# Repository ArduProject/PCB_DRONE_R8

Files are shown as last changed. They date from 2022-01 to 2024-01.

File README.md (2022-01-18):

# Archivos de fabricación de la versión del PCB con STM32F103R8

CURSO_PCB_DRONE

En este repositorio encontrareis los archivos de fabricación y las listas de montaje del PCB con STM32F103**R8** que hemos visto en el curso. Enlace al curso: https://www.udemy.com/course/controlador-de-vuelo-drones-arduino-pcb/?referralCode=FD3F1CBF871EDFD84B6F

La estructura de las carpetas de este repositorio es la misma que hemos visto en el curso: una carpeta GERBER con los archivos de fabricación del PCB, y una carpeta MONTAJE con las listas de componentes y el archivo de colocación de huellas (CURSO_PCB_DRONE-all-pos.xlsx). Tambien se incluye un manual de montaje del PCB y del drone. La única diferencia con el curso es que al descargar el repositorio, dentro de la carpeta MONTAJE encontrareis dos listas en vez de una:

- Lista de componentes (BOM) para cargar en la web de JLCPCB, la lista que hemos generado en el vídeo anterior: CURSO_PCB_DRONE_BOM_JLCPCB.xlsx
- Lista con los componentes que tendremos que comprar y montar en el PCB y el drone (antena SMA, conector de batería XT60, motores, batería...): CURSO_PCB_DRONE_BOM_extra.xlsx

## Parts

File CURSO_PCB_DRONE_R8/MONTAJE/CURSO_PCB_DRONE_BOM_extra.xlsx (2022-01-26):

Id | Referencia esquema | Descripción | Enlace Amazon | Enlace Aliexpress | Necesario para montaje de:
 |  |  |  |  | PCB | DRONE
A1 | J16 | Antena SMA | https://amzn.to/3mPTdu5 | https://s.click.aliexpress.com/e/_9z2YgC | X
A2 | J17 | Conector de batería XT60 | https://amzn.to/3zj09VF | https://s.click.aliexpress.com/e/_Al7UrO | X | X
A3 | U11 | Regulador LM7805 TO-220 | https://amzn.to/3HzEs6F | https://s.click.aliexpress.com/e/_ATJGEc | X
A4 | J2, J4, J6, J7, J8, J9, J10, J11, J12, J13, J14, J15 | Kit conectores 'pin header' macho de 2.54mm | https://amzn.to/3ES77Su | https://s.click.aliexpress.com/e/_9vqOJA | X
A5 | - | Kit conectores 'pin socket' hembra de 2.54mm | https://amzn.to/3qSfYP1 | https://s.click.aliexpress.com/e/_AmZCtw | X | X
A6 | SW4 | Interruptor manual ref. SS-12D00G4 | https://amzn.to/3pXzwlO | https://s.click.aliexpress.com/e/_9zbXPK | X
A7 | J5 | Monitor OLED 0.96' | - | https://s.click.aliexpress.com/e/_AbfWzS | X
A8 | - | Separadores de plástico 6mm M3 | https://amzn.to/3FL1Zkq | https://s.click.aliexpress.com/e/_AnLr04 | X | X
A9 | - | Tuercas de plástico M3 | https://amzn.to/3FL1Zkq | https://s.click.aliexpress.com/e/_ASSfpm | X | X
A10 | - | Tornillos de plástico 4mm M3 | https://amzn.to/3FL1Zkq | https://s.click.aliexpress.com/e/_A4Ar1A | X | X
A11 | - | Kit de 4 motores MT2204 2300KV + ESC 12A + Hélices 5030 | - | https://s.click.aliexpress.com/e/_9x4l8y |  | X
A12 | - | Mando FLYSKY-FS-i6 + receptor iA6B | https://amzn.to/34aDmQd | https://s.click.aliexpress.com/e/_Aa8E8Y |  | X
A13 | - | Frame 250mm | - | https://s.click.aliexpress.com/e/_9jW9De |  | X
A14 | - | Batería Lipo 3S 11.1V 1800mAh 50C XT60 | https://amzn.to/3f0Io4d | https://s.click.aliexpress.com/e/_9uFewy |  | X
A15 | - | LiDAR FT-LUNA | - | https://s.click.aliexpress.com/e/_ALu5SY |  | X
A16 | - | Barómetro MS5611 | https://amzn.to/34iogs3 | https://s.click.aliexpress.com/e/_9ydlqC |  | X
A17 | - | Carcasa MS5611 (modelo 3D) | https://www.thingiverse.com/thing:3460451 |  |  | X
A18 | - | Terminales bala 3.5mm | https://amzn.to/34gPRKd | https://s.click.aliexpress.com/e/_9Qs85a |  | X
A19 | - | Tuerca de acero inox. M3 | - | https://s.click.aliexpress.com/e/_A7q36C |  | X
A20 | - | Tornillo de acero inox. 8mm M3 | - | https://s.click.aliexpress.com/e/_AfkXxE |  | X
A21 | - | Conector terminal anillo RV1.25-3 | - | https://s.click.aliexpress.com/e/_AePFNA |  | X
A22 | - | Cable AWG 30 | https://amzn.to/3qNt8gp | https://s.click.aliexpress.com/e/_97MU5K |  | X

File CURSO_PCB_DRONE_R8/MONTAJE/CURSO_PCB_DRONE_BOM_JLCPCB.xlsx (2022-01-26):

Designator | Footprint | Comment | JLCPCB Part #
Y3 | Crystal_SMD_5032-2Pin_5.0x3.2mm | 8Mhz | C115962
J3,J1 | MICRO-USB-SMD_5P-P0.65-H-F_MICRO5.9MMUSB | USB_B_Micro | C393940
Y2 | Crystal_SMD_3225-4Pin_3.2x2.5mm | 12Mhz | C9002
U7 | TF-SMD_472192001 | MICROSD_C164170 | C164170
U10 | InvenSense_QFN-24_4x4mm_P0.5mm | MPU-6050 | C24112
C43,C28,C29,C30 | C_0402_1005Metric | 10nF | C15195
U4 | LQFP-64_10x10mm_P0.5mm | STM32F103R8T6 | C46034
U1 | SOIC-16_3.9x9.9mm_P1.27mm | CH340G | C14267
C1,C2,C4,C5,C6,C10,C11,C12,C14,C15,C16,C19,C22,C23,C24,C33,C39,C44,C45,C46,C8,C9 | C_0402_1005Metric | 100nF | C1525
C3,C7,C40 | C_0402_1005Metric | 4.7uF | C23733
C13,C27 | C_0402_1005Metric | 1uF | C52923
C17,C18,C35,C36 | C_0402_1005Metric | 12pF | C1547
C20,C21 | C_0402_1005Metric | 33pF | C1562
C25,C26 | C_0402_1005Metric | 20pF | C1554
C31,C32 | C_0402_1005Metric | 10pF | C32949
C34 | C_0402_1005Metric | 33nF | C1585
C37 | C_0402_1005Metric | 1.5pF | C1552
C38 | C_0402_1005Metric | 1pF | C1550
C41,C47 | C_0402_1005Metric | 2.2nF | C1531
C42 | C_0402_1005Metric | 4.7pF | C1569
C48 | C_1206_3216Metric | 0.22uF | C1857
C49 | C_1206_3216Metric | 10uF | C13585
C50,C51 | C_1206_3216Metric | 10uF (t) | C7171
D3,D4,D5,D12,D13 | LED_0603_1608Metric | ROJO | C2286
D6,D7,D15 | LED_0603_1608Metric | AZUL | C72041
D8,D10,D11,D14,D16 | LED_0603_1608Metric | VERDE | C72043
FB1,FB2 | L_0805_2012Metric | 100Ohm @ 100Mhz | C1015
L1 | L_0402_1005Metric | 27nH | C18830
L2 | L_0402_1005Metric | 3.9nH | C14033
L3 | L_0402_1005Metric | 8.2nH | C16208
L4 | L_0402_1005Metric | 2.7nH | C27123
R1,R2 | R_0402_1005Metric | 1k | C11702
R11,R12,R13,R30,R31,R33,R34,R19 | R_0402_1005Metric | 10k | C25744
R14 | R_0402_1005Metric | 1.5k | C25867
R15 | R_0402_1005Metric | 330 | C25104
R20,R21 | R_0603_1608Metric | 1.5k | C22843
R22,R23,R24,R18 | R_0603_1608Metric | 1k | C21190
R25,R26,R27,R28,R39 | R_0402_1005Metric | 4.7k | C25900
R35 | R_0402_1005Metric | 22k | C25768
R36 | R_0402_1005Metric | 1M | C26083
SW1,SW2,SW3 | KEY-TH_2P-L6.0-W3.5-P6.50 | RST | C221867
U2 | TQFP-32_7x7mm | ATMEGA328P-AU | C14877
U3 | SOIC-8_W3.9mm | LM358DR | C7950
U5 | QFN-20-1EP_4x4mm_P0.5mm_EP2.5x2.5mm | nRF24L01P | C8791
U6 | SOIC-20W_7.5x12.8mm_P1.27mm | 74HC245 | C5625
U8 | SOT-23-6 | SRV05-4 | C85364
U9 | SOT-353_SC-70-5 | 74AHC1G125 | C151890
U12 | SOT-223-3_TabPin2 | AMS1117-3.3 | C6186
Y1,Y5 | Crystal_SMD_3225-4Pin_3.2x2.5mm | 16Mhz | C13738
Y4 | Crystal_SMD_2012-2Pin_2.0x1.2mm | 32.768kHz | C97602
R9,R10,R16,R17 | R_0603_1608Metric | 22 | C23345
R37 | R_0603_1608Metric | 4.7k | C23162
R3,R4,R5 | R_0603_1608Metric | 750 | C23241
R6,R7,R8,R38 | R_0603_1608Metric | 220 | C22962
R29 | R_0603_1608Metric | 47k | C25819
R32 | R_0603_1608Metric | 15k | C22809
D1,D2,D9 | D_SOD-123 | B5819W | C8598

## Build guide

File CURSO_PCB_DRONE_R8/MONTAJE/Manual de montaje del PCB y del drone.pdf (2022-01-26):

# Manual de montaje del PCB

No todos los componentes del PCB vienen montados desde JLCPCB. Para reducir el coste del PCB, hay algunos componentes que tenemos que comprar y soldar nosotros mismo en casa. En los siguientes apartados veremos como montar estos componentes. En cada apartado se especifica que componente de la lista CURSO_PCB_DRONE_BOM_extra.xlsx hay que utilizar en cada caso.

## 1- Conectores de señal

El PCB cuenta con varios conectores que tenemos que soldar nosotros mismos. Utilizaremos el mismo tipo de conector en todos los casos (Id. A4). Lo ideal es comprar una o varias tiras de este conector e ir cortándolo y soldándolo a la medida de cada caso:

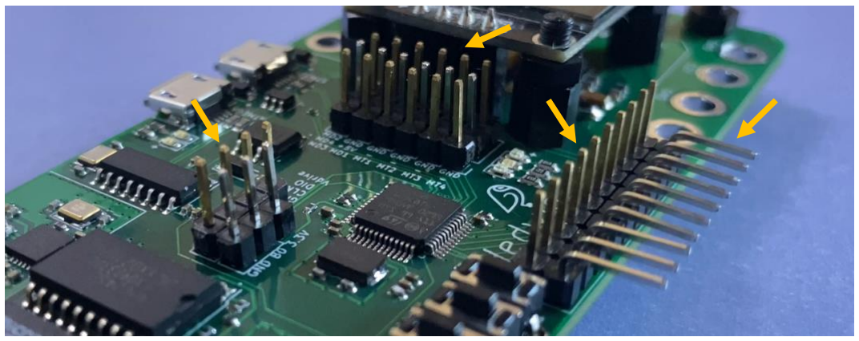
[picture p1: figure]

En lugar del conector con inclinación de 90º se puede utilizar un conector recto como en el resto de los casos.

## 2- Antena SMA

Soldaremos la antena SMA (Id. A1) en su lugar correspondiente. No tiene polaridad, se puede colocar en cualquier orientación. Se puede añadir una antena para aumentar el rango de emisión.

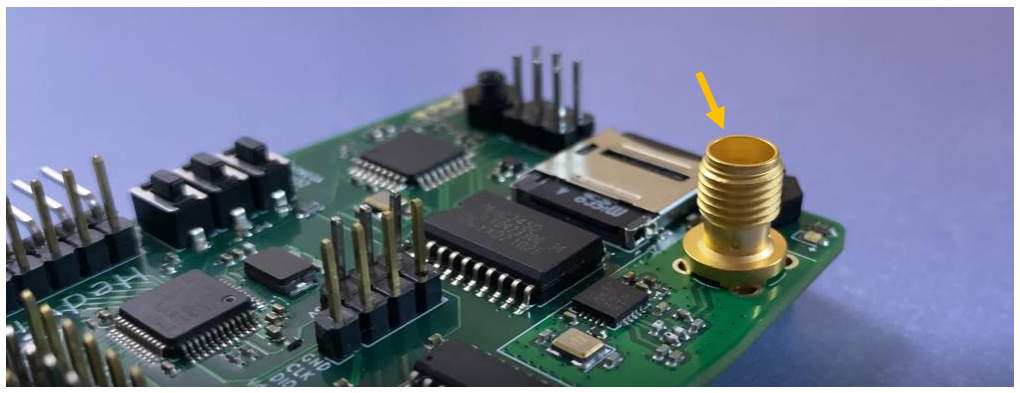
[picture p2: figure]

## 3- Conector XT60 hembra

Utilizaremos un conector XT60 (Id. A2) hembra en el PCB. Hay que garantizar un buen contacto entre el conector y el PCB, la soldadura tiene que ser uniforme, el estaño tiene que rodear todo el conector:

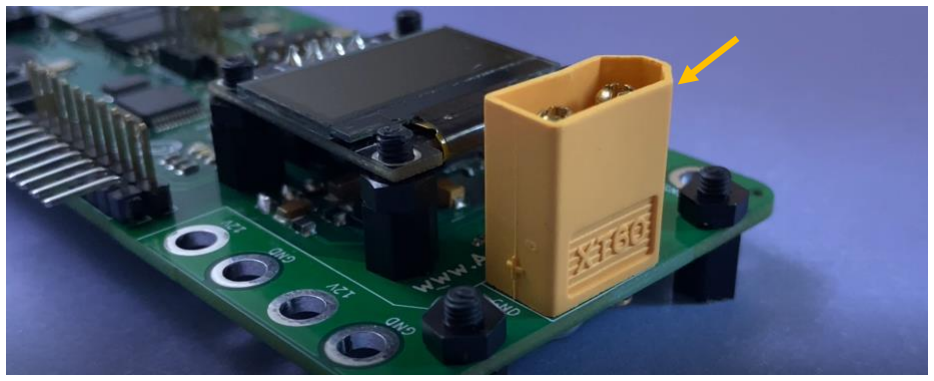
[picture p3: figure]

## 4- Interruptor de 5V para la electrónica

La soldadura de este interruptor (Id. A6) no entraña dificultad, se puede colocar en cualquiera de las dos orientaciones:

## 5- Conector para monitor OLED

No soldar el monitor OLED directamente al PCB. Utilizar un conector de 4 pines hembra (Id. A5) como el de la figura:

## 6- Regulador de 5V y separadores de plástico

Soldar en regulador (Id. A3) en la parte inferior del PCB. El tornillo de plástico que utilizaremos para la sujeción del regulador será a su vez el que sujete uno de los separadores del monitor OLED:

Tornillo

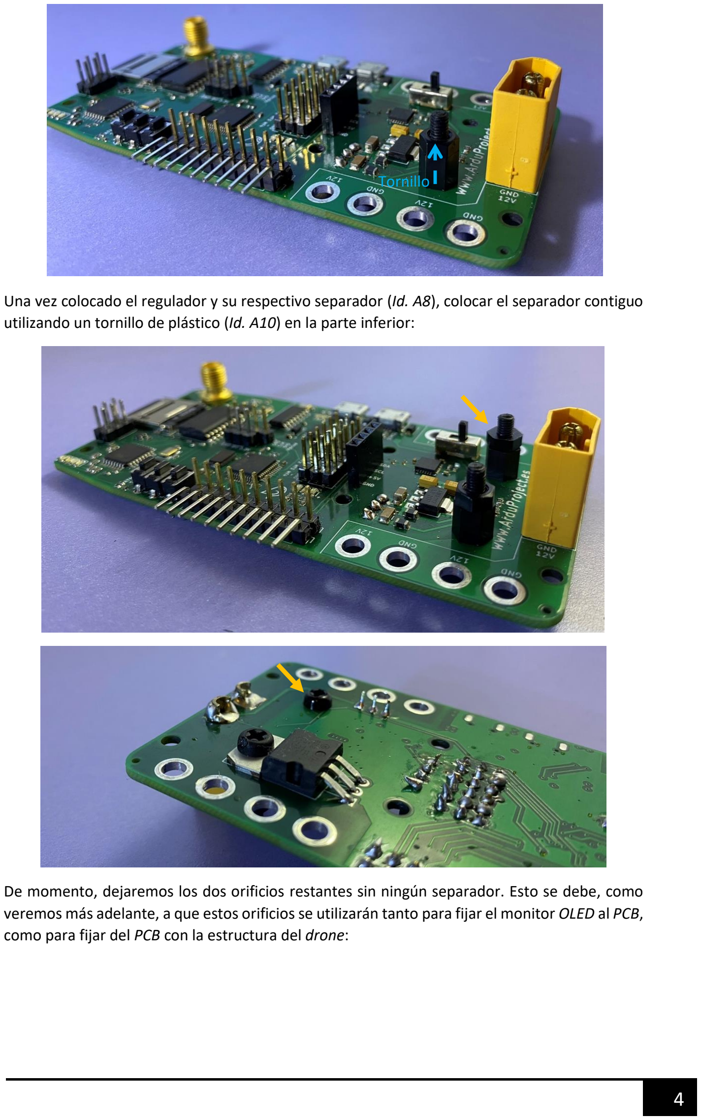
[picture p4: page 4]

Una vez colocado el regulador y su respectivo separador (Id. A8), colocar el separador contiguo utilizando un tornillo de plástico (Id. A10) en la parte inferior:

De momento, dejaremos los dos orificios restantes sin ningún separador. Esto se debe, como veremos más adelante, a que estos orificios se utilizarán tanto para fijar el monitor OLED al PCB, como para fijar del PCB con la estructura del drone:

Tornillo

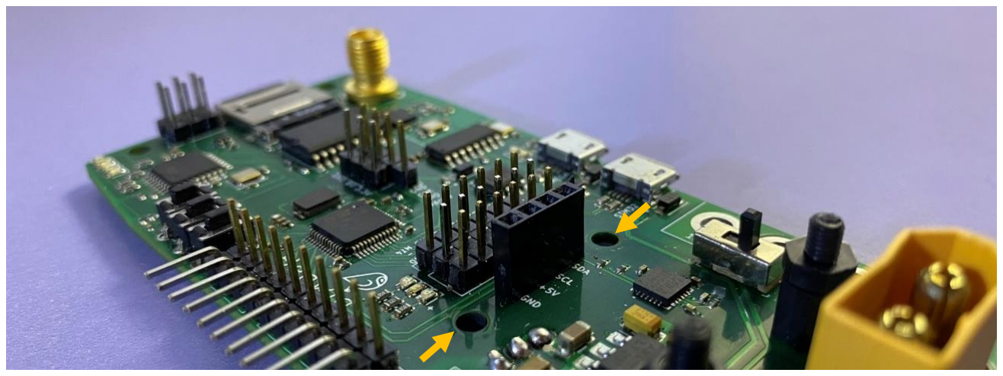
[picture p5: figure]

# Manual de montaje del drone

A lo largo de los siguientes apartadores veremos como integrar todos los componentes del
drone. | En | cada | apartado | se | especifica | que | componente | de | la | lista
CURSO_PCB_DRONE_BOM_extra.xlsx hay que utilizar en cada caso.

La estructura del drone que se va a utilizar tiene dos niveles. Para este proyecto, solo se ha utilizado el nivel inferior:

## 7- Fijación del PCB a la estructura

Hay 6 puntos de fijación del PCB con la estructura del drone (Id. A13). En primer lugar, colocar 6 separadores de plástico en las posiciones indicadas en la figura inferior. Hay que utilizar tornillos de plástico en la parte inferior de la estructura para la fijación de los separadores:

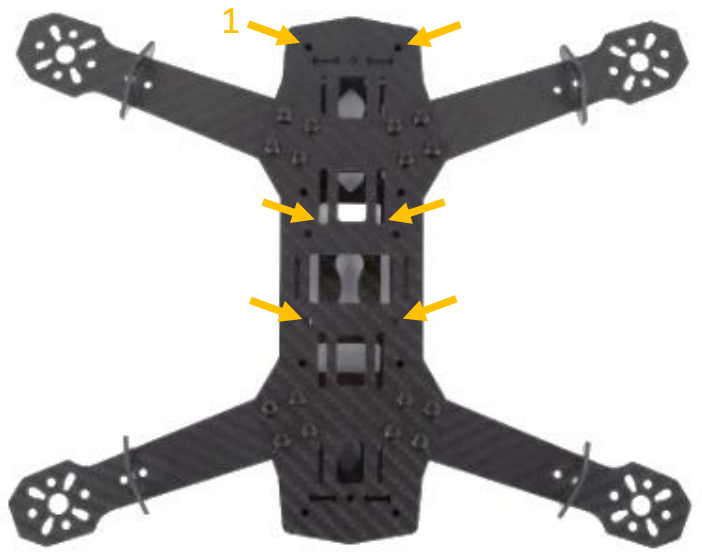
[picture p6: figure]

Una vez hecho esto, encajar el PCB sobre los separadores de plástico fijándonos en colocar el extremo marcado con el número 1 donde corresponde:

1

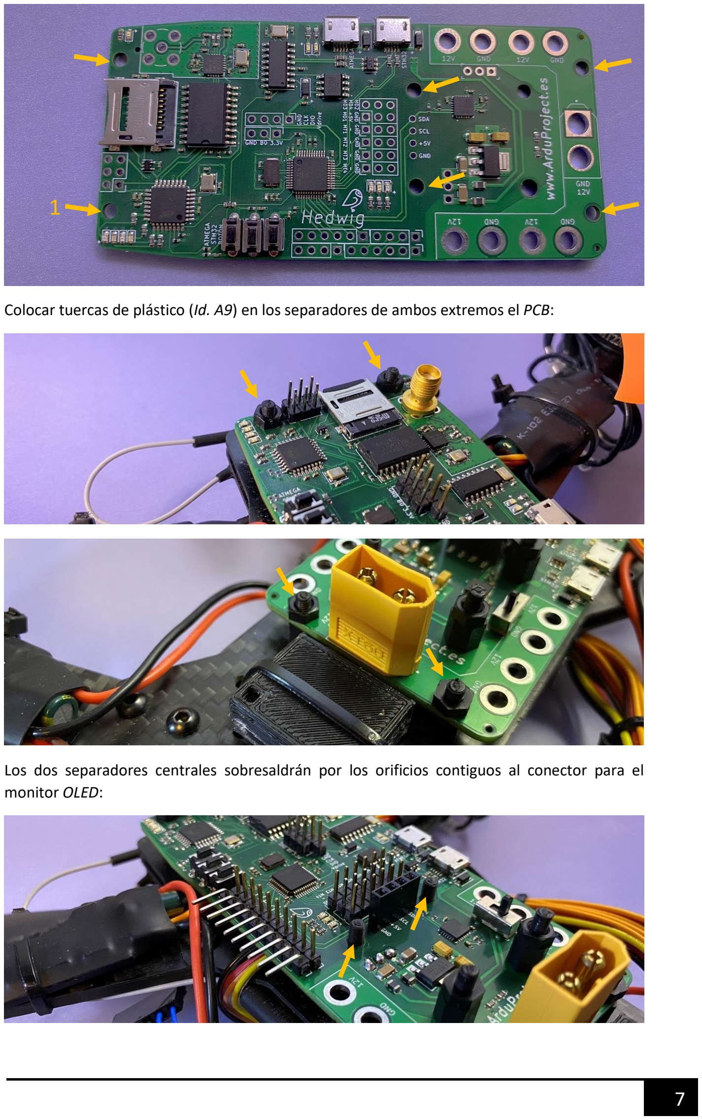
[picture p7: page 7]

Colocar tuercas de plástico (Id. A9) en los separadores de ambos extremos el PCB:

Los dos separadores centrales sobresaldrán por los orificios contiguos al conector para el monitor OLED:

Colocar dos nuevos separadores sobre estos últimos, que se utilizarán para fijar el monitor OLED al PCB:

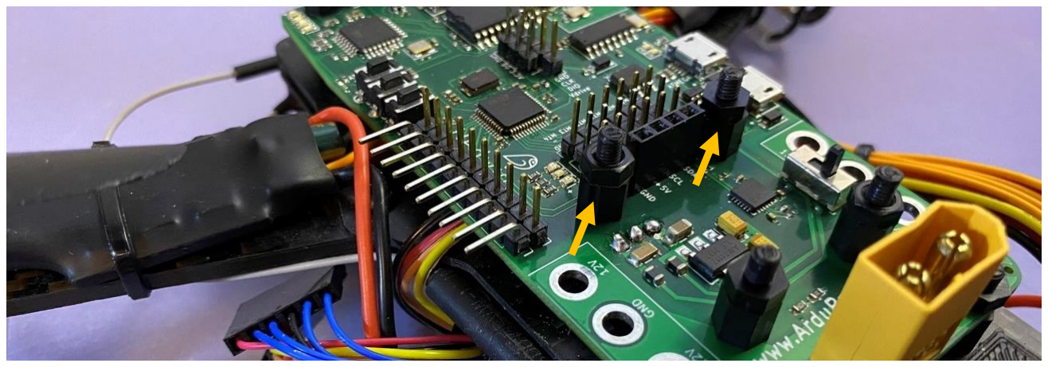
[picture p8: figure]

## 8- Monitor OLED

Una vez colocados tanto el conector hembra de 4 posiciones como los cuatro separadores de plástico, podemos colocar el monitor OLED (Id. A7) en su posición definitiva:

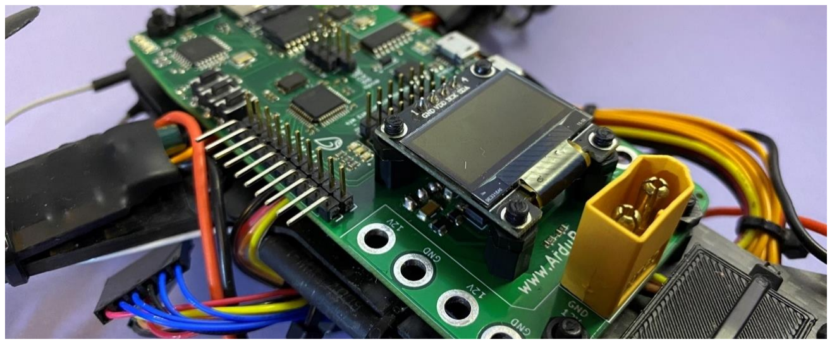
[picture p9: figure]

Es posible que los separadores de plástico de 6mm no sean lo suficientemente altos como para llegar a la altura del conector hembra de 4 posiciones. En ese caso, se pueden utilizar las tuercas de plástico para ganar altura como en la siguiente figura:

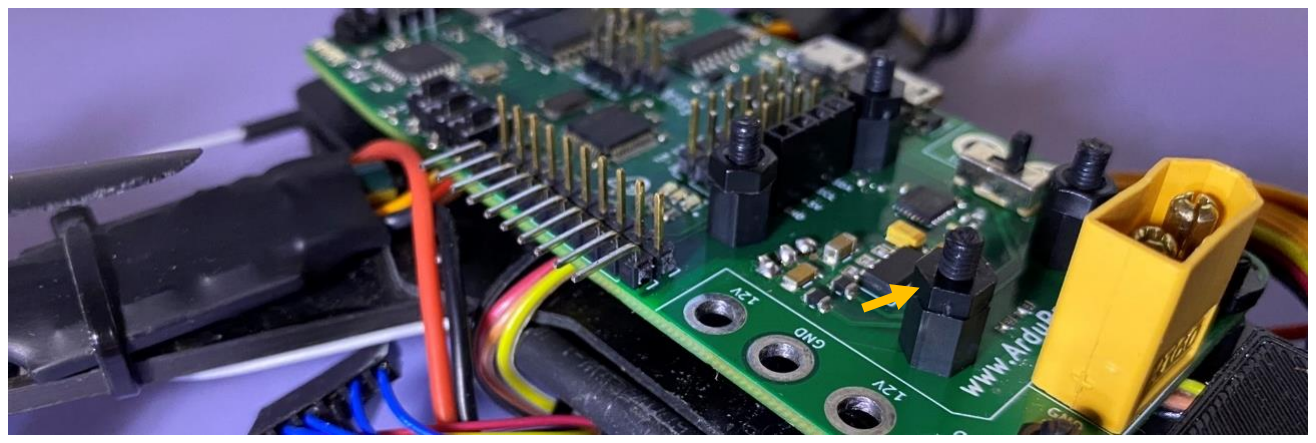
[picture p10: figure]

## 9- Instalación de motores y ESC

En primer lugar, atornillas los cuatro motores (Id. A11) a la estructura del drone:

Colocar cada uno de los cuatro ESC (Id. A11) en cada brazo de la estructura, y sujetar con bridas:

La conexión trifásica entre el ESC y el motor se hará utilizando terminales tipo bala (Id. A18). Soldar cada fase del motor a un terminal macho, y cada cable del ESC a un terminal hembra. Importante utilizar los aislantes de plástico para evitar que las diferentes fases entren en contacto:

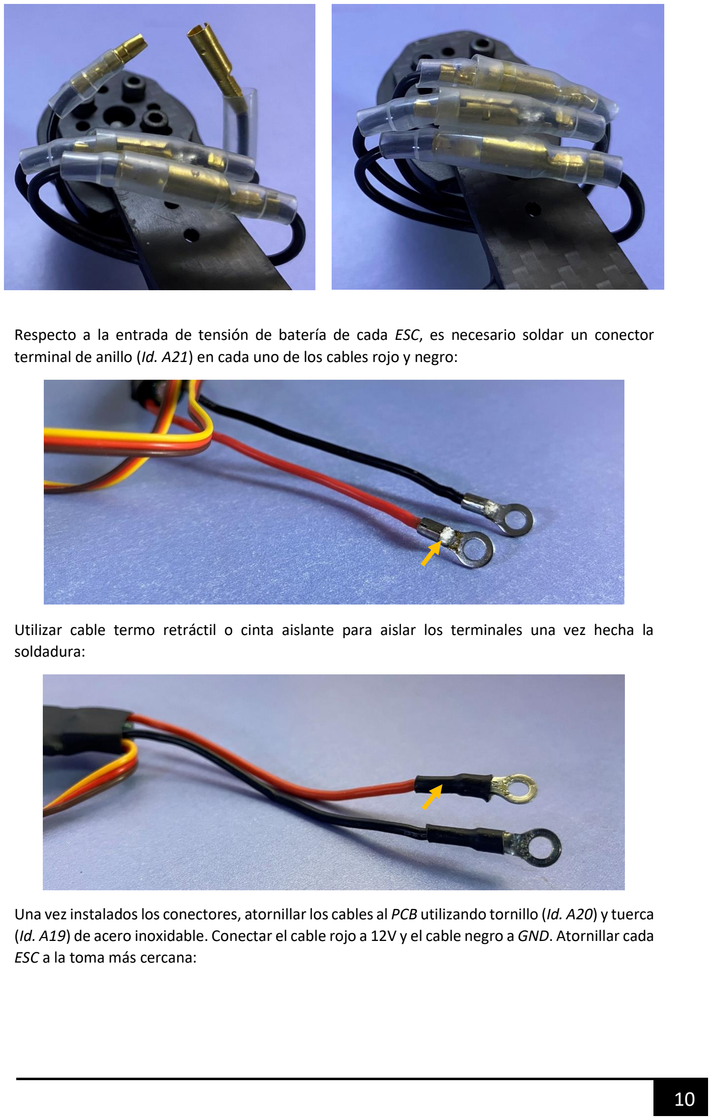
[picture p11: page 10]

Respecto a la entrada de tensión de batería de cada ESC, es necesario soldar un conector terminal de anillo (Id. A21) en cada uno de los cables rojo y negro:

Utilizar cable termo retráctil o cinta aislante para aislar los terminales una vez hecha la soldadura:

Una vez instalados los conectores, atornillarlos cables al PCB utilizando tornillo (Id. A20) y tuerca (Id. A19) de acero inoxidable. Conectar el cable rojo a 12V y el cable negro a GND. Atornillar cada ESC a la toma más cercana:

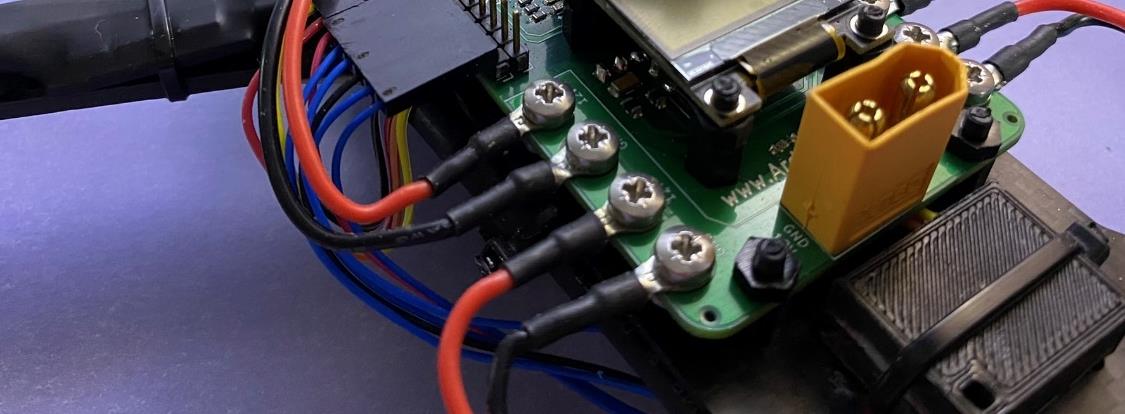
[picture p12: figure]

El cable de señal de cada ESC puede ser conectado directamente al PCB si tener que manipularlo, siempre fijándonos en conectarlo de forma adecuada:

A la hora de conectar los cuatro cables de señal de los cuatro ESC, es importante conectar los motores según esta numeración. Con esto garantizamos que el software proporcionado funcionará correctamente. Con esta numeración, la parte ‘delantera’ de nuestro drone será la marcada con la flecha naranja:

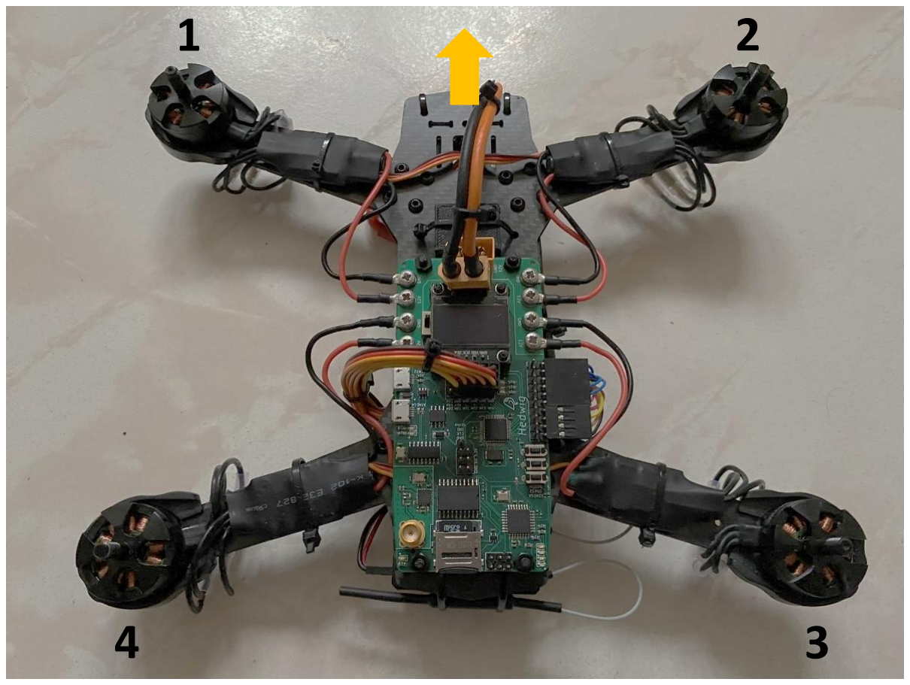
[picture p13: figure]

Conectar el cable de señal del motor 1 de la figura al conector MT1 del PCB

Conectar el cable de señal del motor 2 de la figura al conector MT2 del PCB Conectar el cable de señal del motor 3 de la figura al conector MT3 del PCB Conectar el cable de señal del motor 4 de la figura al conector MT4 del PCB

## 10- Instalación de receptor radio control

La ubicación más lógica para el receptor (Id. A12) es en la parte baja de la estructura, justo debajo del conector para la tarjeta microSD. Sujetar bien el receptor a la estructura utilizando bridas:

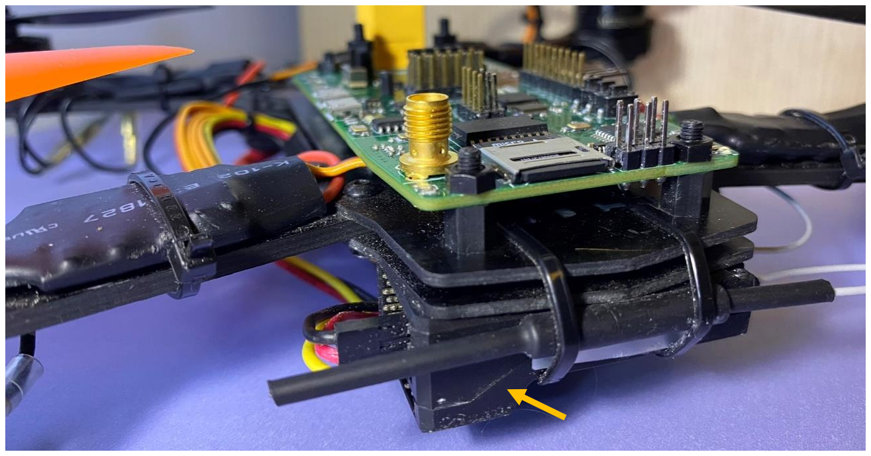
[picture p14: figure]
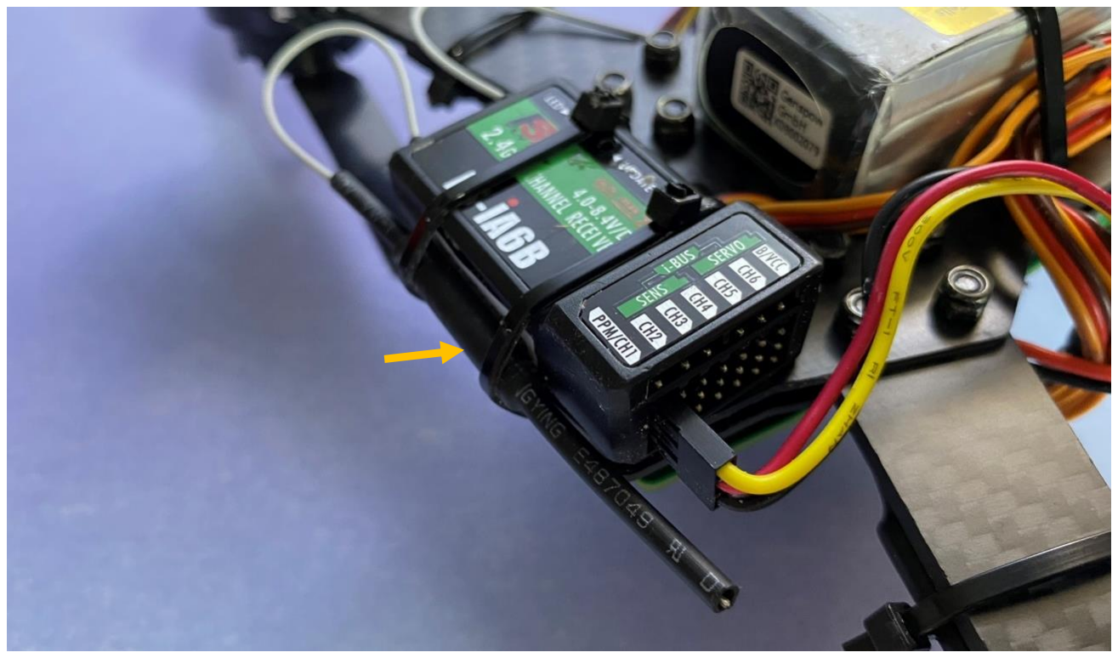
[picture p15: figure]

El fabricante recomienda colocar las dos antenas con una inclinación de 90º. Para ello, colocar la primera antena sobre el propio receptor aprovechando las bridas de sujeción como se muestra la figura superior, y colocar la segunda antena en el extremo contiguo de la estructura, como muestra la imagen inferior:

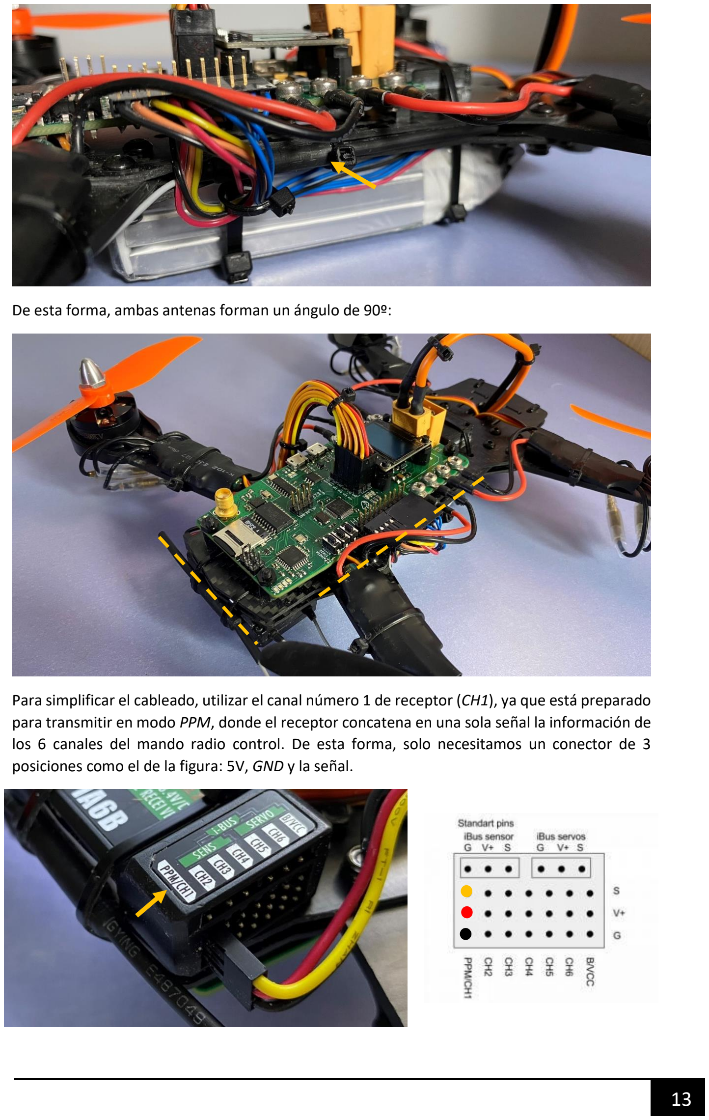
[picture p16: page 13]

De esta forma, ambas antenas forman un ángulo de 90º:

Para simplificar el cableado, utilizar el canal número 1 de receptor (CH1), ya que está preparado para transmitir en modo PPM, donde el receptor concatena en una sola señal la información de los 6 canales del mando radio control. De esta forma, solo necesitamos un conector de 3 posiciones como el de la figura: 5V, GND y la señal.

Conectaremos el otro extremo de este conector al PCB, también al canal número 1 (MD1).

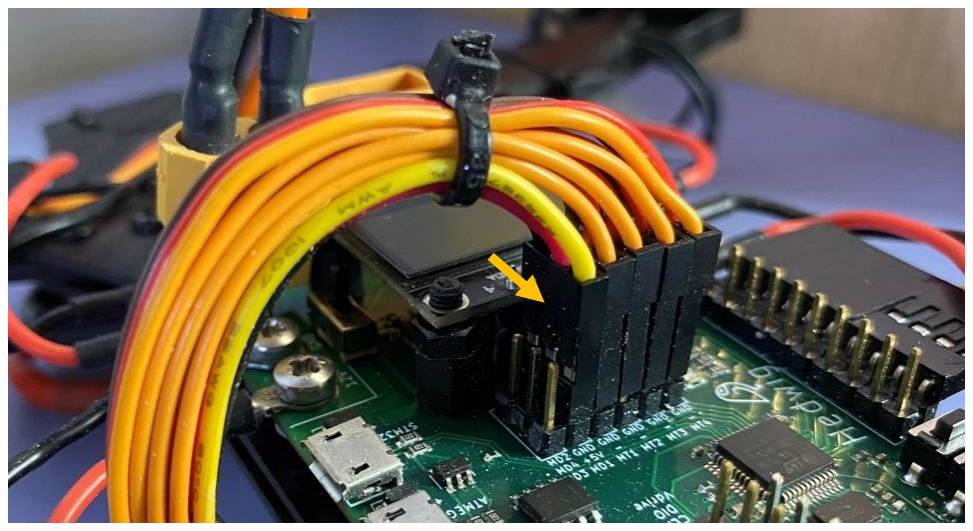
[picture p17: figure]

## 11- Instalación de la batería

Colocar la batería (Id. A14) en la parte inferior del drone. Al ser el elemento más pesado de todos, conviene centrar la batería lo máximo posible en la estructura:

Si los cables de la batería son demasiado cortos como para llegar al conector XT60 del PCB, habrá que alargarlos. Utilizar cable de la misma sección que el de la batería y aislad bien los cables, hay que evitar a toda costa hacer un cortocircuito en la batería:

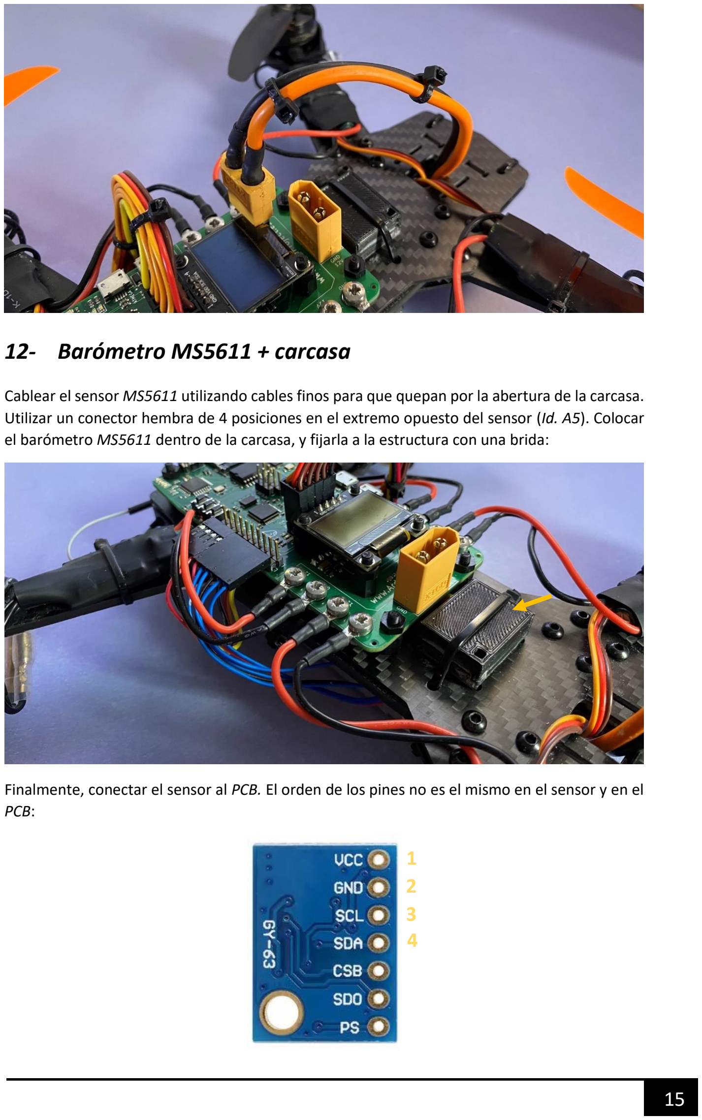
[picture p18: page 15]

## 12- Barómetro MS5611 + carcasa

Cablear el sensor MS5611 utilizando cables finos para que quepan por la abertura de la carcasa. Utilizar un conector hembra de 4 posiciones en el extremo opuesto del sensor (Id. A5). Colocar el barómetro MS5611 dentro de la carcasa, y fijarla a la estructura con una brida:

Finalmente, conectar el sensor al PCB. El orden de los pines no es el mismo en el sensor y en el PCB:

1
2
3
4

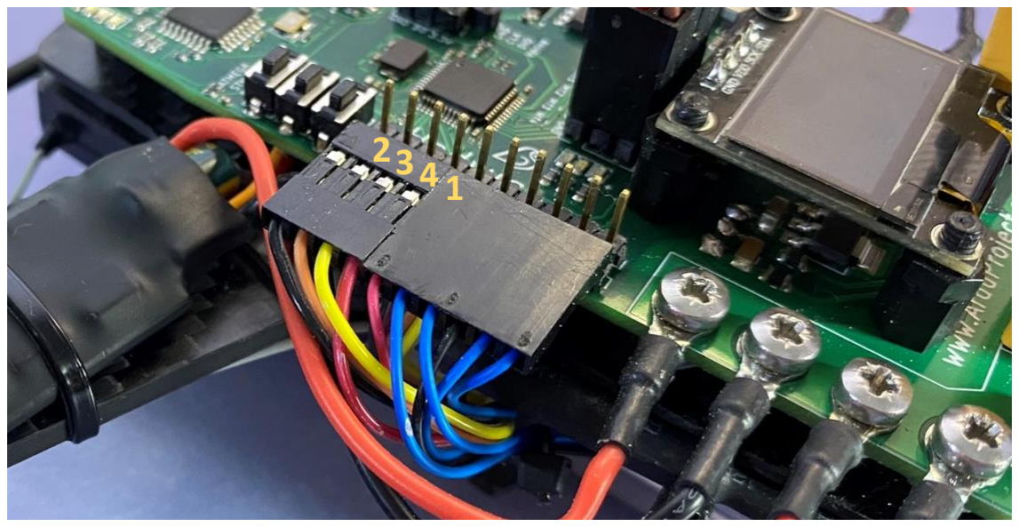
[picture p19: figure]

## 13- LiDAR

Colocar el LiDAR (Id. A15) en el extremo inferior del PCB opuesto al receptor radio control y fijarlo utilizando dos bridas a los dos orificios contiguos a este:

El conector de este no es compatible con nuestro PCB (es una mejora interesante que podéis añadir al PCB vosotros mismos). Por ello, hay que cortar los cables y utilizar un conector hembra de 6 posiciones (Id. A5).

La numeración de nuestro conector es idéntica a la delmódulo LiDAR. De todas formas, asegurad que conectáis el conector de forma correcta:

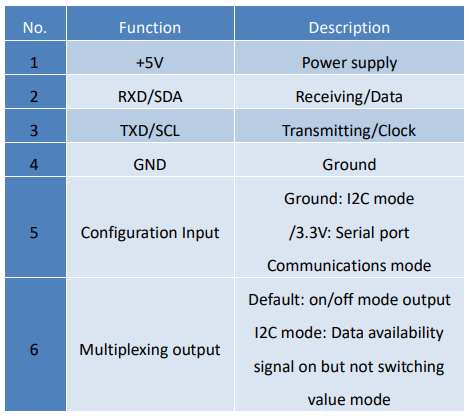
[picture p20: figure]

Hay que conector los pines 1-6 del módulo LiDAR con estos pines del PCB:

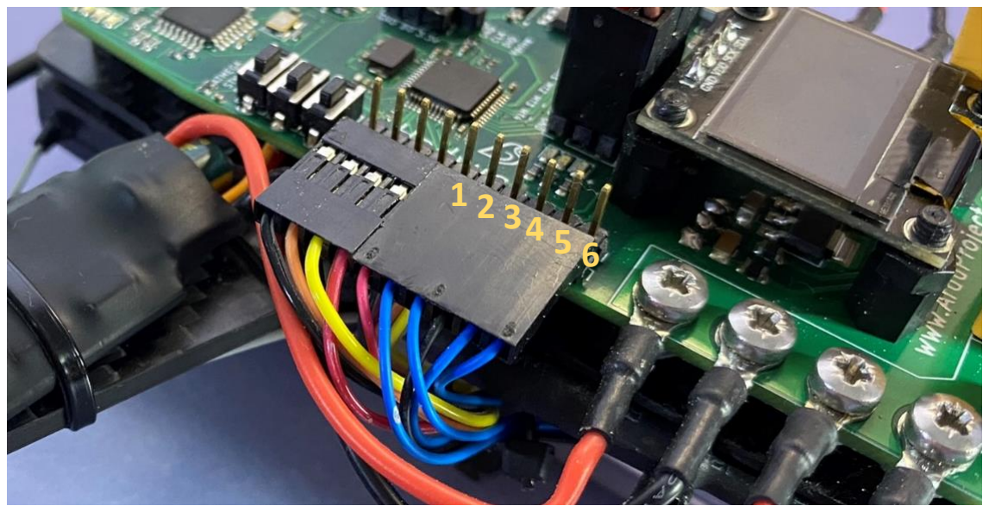
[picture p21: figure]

Los siguientes dos apartados tienen que realizarse una vez completado el montaje de los apartados superiores. Es necesario haber validado la comunicación con el mando RC.

## 14- Sentido de giro de los motores

De los cuatro motores que tenemos, dos de ellos tienen que girar en un sentido, y los otros dos en el otro sentido. Los motores en diagonal tienen que girar siempre en el mismo sentido:

Para cambiar el sentido de giro de un motor, basta con intercambiar dos de sus fases. Gracias a los terminales bala que hemos utilizado, será muy sencillo hacer el intercambio de las fases:

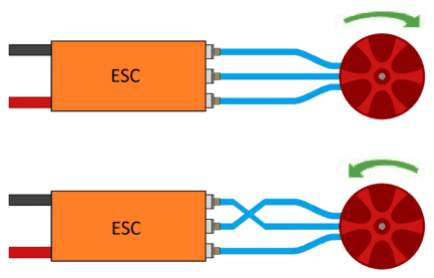
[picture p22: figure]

Comenzar conectando las fases de los motores y ESC de forma aleatoria. Poner los motores a girar (sin hélices) y ver en qué sentido lo hacen. Después, ir intercambiado las fases de aquellos motores que giren en sentido contrario al deseado, hasta que todos giren en el sentido especificado en la figura superior.

Tenéis el software para girar los motores en mi GitHub. (https://github.com/ArduProject/PCB_DRONE_VALIDACION_BASICA)

## 15- Colocación de las hélices

La colocación de las hélices tiene que hacerse en último lugar, tras haber montado el drone, y haber comprobado que el software actúa como debería. Nunca colocar las hélices sin haber validado antes el software.

Os habréis fijado en que las palas de las hélices tienen inclinación:

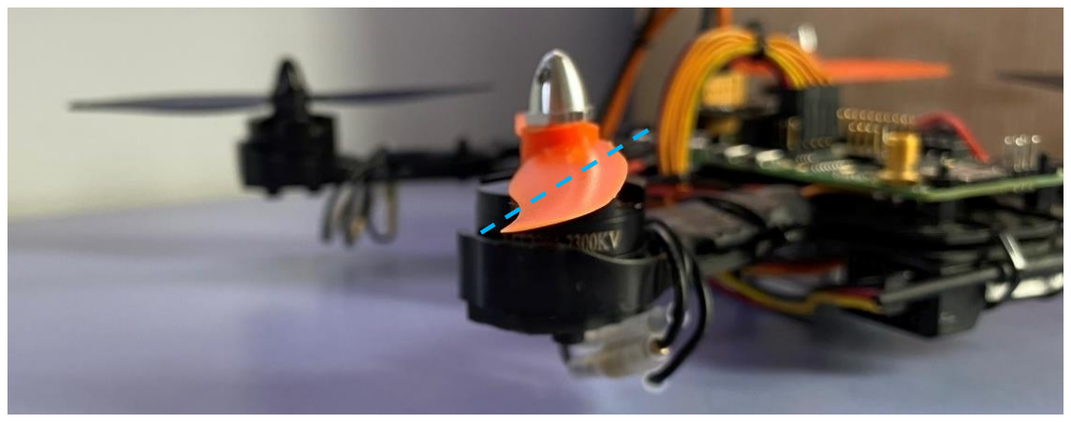
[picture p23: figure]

La parte alta de la pala siempre tiene que apuntar en sentido del movimiento. Esta es la razón de tener dos tipos de hélice diferentes. Colocar las cuatro hélices siguiendo esta lógica y teniendo en cuenta el sentido de giro de cada motor como se especifica en el apartado anterior:

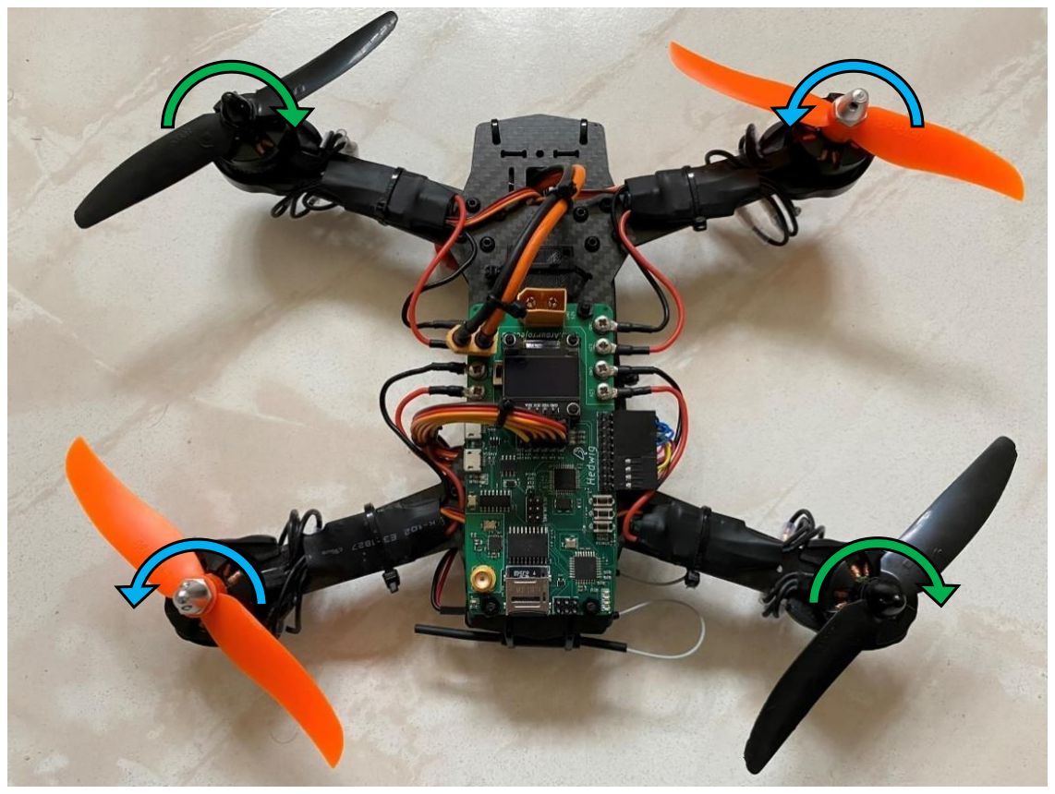
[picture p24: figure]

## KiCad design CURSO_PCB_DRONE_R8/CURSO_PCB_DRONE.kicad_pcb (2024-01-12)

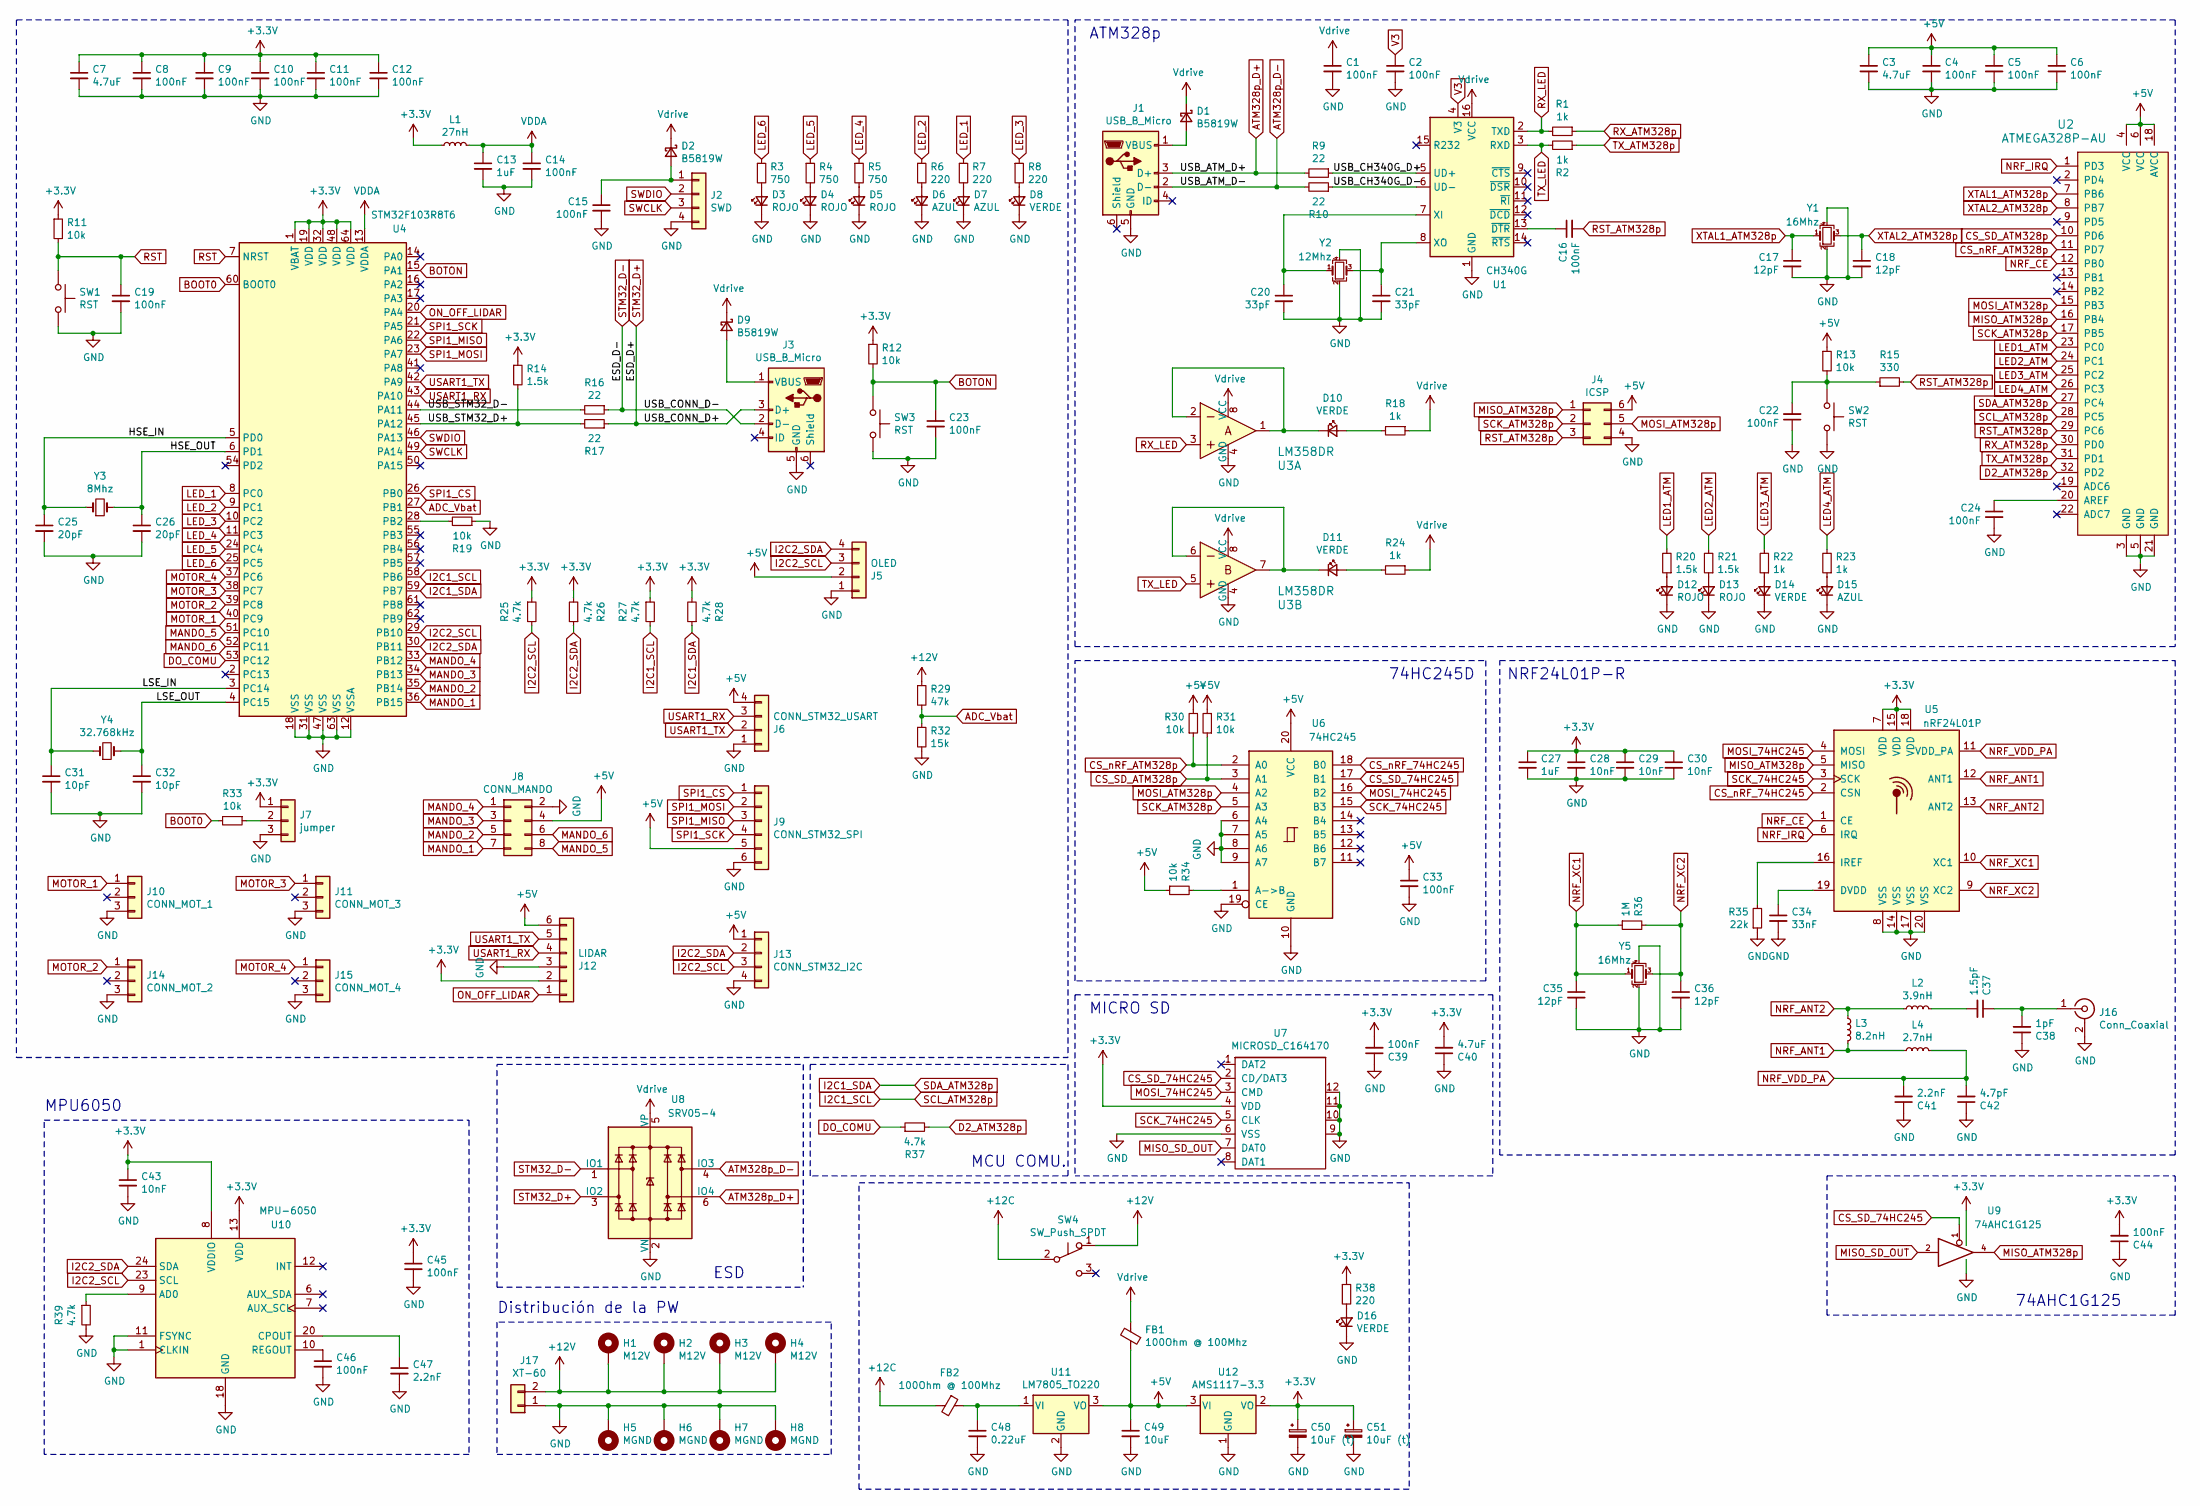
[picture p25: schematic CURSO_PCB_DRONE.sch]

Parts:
C1, C2, C4, C5, C6, C8, C9, C10, C11, C12, C14, C15, C16, C19, C22, C23, C24, C33, C39, C44, C45, C46: 100nF; C_0402_1005Metric
C3, C7, C40: 4.7uF; C_0402_1005Metric
C13, C27: 1uF; C_0402_1005Metric
C17, C18, C35, C36: 12pF; C_0402_1005Metric
C20, C21: 33pF; C_0402_1005Metric
C25, C26: 20pF; C_0402_1005Metric
C28, C29, C30, C43: 10nF; C_0402_1005Metric
C31, C32: 10pF; C_0402_1005Metric
C34: 33nF; C_0402_1005Metric
C37: 1.5pF; C_0402_1005Metric
C38: 1pF; C_0402_1005Metric
C41, C47: 2.2nF; C_0402_1005Metric
C42: 4.7pF; C_0402_1005Metric
C48: 0.22uF; C_1206_3216Metric
C49: 10uF; C_1206_3216Metric
C50, C51: 10uF (t); C_1206_3216Metric
D1, D2, D9: B5819W; D_SOD-123
D3, D4, D5, D12, D13: ROJO; LED_0603_1608Metric
D6, D7, D15: AZUL; LED_0603_1608Metric
D8, D10, D11, D14, D16: VERDE; LED_0603_1608Metric
FB1, FB2: 100Ohm @ 100Mhz; L_0805_2012Metric
H1, H2, H3, H4: M12V; MountingHole_3.5mm_5.5mm
H5, H6, H7, H8: MGND; MountingHole_3.5mm_5.5mm
J1, J3: USB_B_Micro; MICRO-USB-SMD_5P-P0.65-H-F_MICRO5.9MMUSB
J2: SWD; PinHeader_1x04_P2.54mm_Vertical
J4: ICSP; PinHeader_2x03_P2.54mm_Vertical
J5: OLED
J6: CONN_STM32_USART; PinHeader_1x04_P2.54mm_Horizontal
J7: jumper; PinHeader_1x03_P2.54mm_Vertical
J8: CONN_MANDO; PinHeader_2x04_P2.54mm_Vertical
J9: CONN_STM32_SPI; PinHeader_1x06_P2.54mm_Vertical
J10: CONN_MOT_1; PinHeader_1x03_P2.54mm_Vertical
J11: CONN_MOT_3; PinHeader_1x03_P2.54mm_Vertical
J12: LIDAR; PinHeader_1x06_P2.54mm_Horizontal
J13: CONN_STM32_I2C; PinHeader_1x04_P2.54mm_Vertical
J14: CONN_MOT_2; PinHeader_1x03_P2.54mm_Vertical
J15: CONN_MOT_4; PinHeader_1x03_P2.54mm_Vertical
J16: Conn_Coaxial; SMA_142-0701-201
J17: XT-60; AMASS_XT60-M
L1: 27nH; L_0402_1005Metric
L2: 3.9nH; L_0402_1005Metric
L3: 8.2nH; L_0402_1005Metric
L4: 2.7nH; L_0402_1005Metric
R1, R2: 1k; R_0402_1005Metric
R3, R4, R5: 750; R_0603_1608Metric
R6, R7, R8, R38: 220; R_0603_1608Metric
R9, R10, R16, R17: 22; R_0603_1608Metric
R11, R12, R13, R19, R30, R31, R33, R34: 10k; R_0402_1005Metric
R14: 1.5k; R_0402_1005Metric
R15: 330; R_0402_1005Metric
R18, R22, R23, R24: 1k; R_0603_1608Metric
R20, R21: 1.5k; R_0603_1608Metric
R25, R26, R27, R28, R39: 4.7k; R_0402_1005Metric
R29: 47k; R_0603_1608Metric
R32: 15k; R_0603_1608Metric
R35: 22k; R_0402_1005Metric
R36: 1M; R_0402_1005Metric
R37: 4.7k; R_0603_1608Metric
SW1, SW2, SW3: RST; KEY-TH_2P-L6.0-W3.5-P6.50
SW4: SW_Push_SPDT; Switch_Slide
U1: CH340G; SOIC-16_3.9x9.9mm_P1.27mm
U2: ATMEGA328P-AU; TQFP-32_7x7mm; MPN ATMEGA328P-AU; Digi-Key_PN ATMEGA328P-AU-ND
U3: LM358DR; SOIC-8_W3.9mm; MPN LM358DR; Digi-Key_PN 296-1014-1-ND
U4: STM32F103R8T6; LQFP-64_10x10mm_P0.5mm
U5: nRF24L01P; QFN-20-1EP_4x4mm_P0.5mm_EP2.5x2.5mm
U6: 74HC245; SOIC-20W_7.5x12.8mm_P1.27mm
U7: MICROSD_C164170; TF-SMD_472192001
U8: SRV05-4; SOT-23-6
U9: 74AHC1G125; SOT-353_SC-70-5
U10: MPU-6050; InvenSense_QFN-24_4x4mm_P0.5mm
U11: LM7805_TO220; TO-220-3_Horizontal_TabDown
U12: AMS1117-3.3; SOT-223-3_TabPin2
Y1, Y5: 16Mhz; Crystal_SMD_3225-4Pin_3.2x2.5mm
Y2: 12Mhz; Crystal_SMD_3225-4Pin_3.2x2.5mm
Y3: 8Mhz; Crystal_SMD_5032-2Pin_5.0x3.2mm
Y4: 32.768kHz; Crystal_SMD_2012-2Pin_2.0x1.2mm

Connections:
+3V3: C7.1, C8.1, C9.1, C10.1, C11.1, C12.1, C27.1, C28.1, C29.1, C30.1, C39.2, C40.2, C43.1, C44.2, C45.1, C50.1, C51.1, J7.1, J12.2, L1.1, R11.1, R12.1, R14.1, R25.1, R26.2, R27.1, R28.2, R38.1, U4.1 (VBAT), U4.19 (VDD), U4.32 (VDD), U4.48 (VDD), U4.64 (VDD), U5.7 (VDD), U5.15 (VDD), U5.18 (VDD), U7.4 (VDD), U9.5 (VCC), U10.8 (VDDIO), U10.13 (VDD), U12.2 (VO)
+5V: C3.1, C4.1, C5.1, C6.1, C33.1, C49.1, FB1.1, J4.6, J5.2, J6.4, J8.4, J9.5, J12.6, J13.1, R13.1, R30.2, R31.2, R34.1, U2.4 (VCC), U2.6 (VCC), U2.18 (AVCC), U6.20 (VCC), U11.3 (VO), U12.3 (VI)
+12C: FB2.2, SW4.2 (B)
+12V: H1.1, H2.1, H3.1, H4.1, J17.2, R29.1, SW4.1 (A)
/HSE_IN: C25.1, U4.5 (PD0), Y3.1
/HSE_OUT: C26.1, U4.6 (PD1), Y3.2
/LSE_IN: C31.1, U4.3 (PC14), Y4.1
/LSE_OUT: C32.1, U4.4 (PC15), Y4.2
/USB_CH340G_D+: R9.1, U1.5 (UD+)
/USB_CH340G_D-: R10.1, U1.6 (UD-)
/USB_STM32_D+: R14.2, R17.2, U4.45 (PA12)
/USB_STM32_D-: R16.2, U4.44 (PA11)
ADC_Vbat: R29.2, R32.1, U4.27 (PB1)
ATM328p_D+: J1.3 (D+), R9.2, U8.6 (IO4)
ATM328p_D-: J1.2 (D-), R10.2, U8.4 (IO3)
BOOT0: R33.2, U4.60 (BOOT0)
BOTON: C23.1, R12.2, SW3.1, U4.15 (PA1)
CS_SD_74HC245: U6.17 (B1), U7.2 (CD/DAT3), U9.1
CS_SD_ATM328p: R31.1, U2.10 (PD6), U6.3 (A1)
CS_nRF_74HC245: U5.2 (CSN), U6.18 (B0)
CS_nRF_ATM328p: R30.1, U2.11 (PD7), U6.2 (A0)
D2_ATM328p: R37.2, U2.32 (PD2)
DO_COMU: R37.1, U4.53 (PC12)
GND: C1.2, C2.2, C3.2, C4.2, C5.2, C6.2, C7.2, C8.2, C9.2, C10.2, C11.2, C12.2, C13.2, C14.2, C15.2, C17.2, C18.2, C19.2, C20.2, C21.2, C22.1, C23.2, C24.2, C25.2, C26.2, C27.2, C28.2, C29.2, C30.2, C31.2, C32.2, C33.2, C34.2, C35.2, C36.2, C38.1, C39.1, C40.1, C41.1, C42.1, C43.2, C44.1, C45.2, C46.2, C47.2, C48.2, C49.2, C50.2, C51.2, D3.1 (K), D4.1 (K), D5.1 (K), D6.1 (K), D7.1 (K), D8.1 (K), D12.1 (K), D13.1 (K), D14.1 (K), D15.1 (K), D16.1 (K), H5.1, H6.1, H7.1, H8.1, J1.5 (GND), J2.4, J3.5 (GND), J4.4, J5.1, J6.1, J7.3, J8.2, J9.6, J10.3, J11.3, J12.3, J13.4, J14.3, J15.3, J16.2 (Ext), J17.1, R19.1, R32.2, R35.1, R39.2, SW1.2, SW2.2, SW3.2, U1.1 (GND), U2.3 (GND), U2.5 (GND), U2.21 (GND), U3.4 (GND), U4.12 (VSSA), U4.18 (VSS), U4.31 (VSS), U4.47 (VSS), U4.63 (VSS), U5.8 (VSS), U5.14 (VSS), U5.17 (VSS), U5.20 (VSS), U6.6 (A4), U6.7 (A5), U6.8 (A6), U6.9 (A7), U6.10 (GND), U6.19 (CE), U7.6 (VSS), U7.9, U7.10, U7.11, U7.12, U8.2 (VN), U9.3 (GND), U10.1 (CLKIN), U10.11 (FSYNC), U10.18 (GND), U11.2 (GND), U12.1 (GND), Y1.2, Y1.4, Y2.2, Y2.4, Y5.2, Y5.4
I2C1_SCL: R27.2, U2.28 (PC5), U4.58 (PB6)
I2C1_SDA: R28.1, U2.27 (PC4), U4.59 (PB7)
I2C2_SCL: J5.3, J13.3, R25.2, U4.29 (PB10), U10.23 (SCL)
I2C2_SDA: J5.4, J13.2, R26.1, U4.30 (PB11), U10.24 (SDA)
LED1_ATM: R20.2, U2.23 (PC0)
LED2_ATM: R21.2, U2.24 (PC1)
LED3_ATM: R22.2, U2.25 (PC2)
LED4_ATM: R23.2, U2.26 (PC3)
LED_1: R7.1, U4.8 (PC0)
LED_2: R6.1, U4.9 (PC1)
LED_3: R8.1, U4.10 (PC2)
LED_4: R5.1, U4.11 (PC3)
LED_5: R4.1, U4.24 (PC4)
LED_6: R3.1, U4.25 (PC5)
MANDO_1: J8.7, U4.36 (PB15)
MANDO_2: J8.5, U4.35 (PB14)
MANDO_3: J8.3, U4.34 (PB13)
MANDO_4: J8.1, U4.33 (PB12)
MANDO_5: J8.8, U4.51 (PC10)
MANDO_6: J8.6, U4.52 (PC11)
MISO_ATM328p: J4.1, U2.16 (PB4), U5.5 (MISO), U9.4
MISO_SD_OUT: U7.7 (DAT0), U9.2
MOSI_74HC245: U5.4 (MOSI), U6.16 (B2), U7.3 (CMD)
MOSI_ATM328p: J4.5, U2.15 (PB3), U6.4 (A2)
MOTOR_1: J10.1, U4.40 (PC9)
MOTOR_2: J14.1, U4.39 (PC8)
MOTOR_3: J11.1, U4.38 (PC7)
MOTOR_4: J15.1, U4.37 (PC6)
NRF_ANT1: L3.2, L4.1, U5.12 (ANT1)
NRF_ANT2: L2.1, L3.1, U5.13 (ANT2)
NRF_CE: U2.12 (PB0), U5.1 (CE)
NRF_IRQ: U2.1 (PD3), U5.6 (IRQ)
NRF_VDD_PA: C41.2, C42.2, L4.2, U5.11 (VDD_PA)
NRF_XC1: C35.1, R36.1, U5.10 (XC1), Y5.1
NRF_XC2: C36.1, R36.2, U5.9 (XC2), Y5.3
unnamed: C15.1, D2.2 (A), J2.1
unnamed: C16.1, U1.13 (~DTR)
unnamed: C20.1, U1.7 (XI), Y2.1
unnamed: C21.1, U1.8 (XO), Y2.3
unnamed: C22.2, R13.2, R15.1, SW2.1
unnamed: C24.1, U2.20 (AREF)
unnamed: C34.1, U5.19 (DVDD)
unnamed: C37.1, C38.2, J16.1 (In)
unnamed: C37.2, L2.2
unnamed: C46.1, U10.10 (REGOUT)
unnamed: C47.1, U10.20 (CPOUT)
unnamed: C48.1, FB2.1, U11.1 (VI)
unnamed: D1.2 (A), J1.1 (VBUS)
unnamed: D3.2 (A), R3.2
unnamed: D4.2 (A), R4.2
unnamed: D5.2 (A), R5.2
unnamed: D6.2 (A), R6.2
unnamed: D7.2 (A), R7.2
unnamed: D8.2 (A), R8.2
unnamed: D9.2 (A), J3.1 (VBUS)
unnamed: D10.1 (K), U3.1, U3.2
unnamed: D10.2 (A), R18.2
unnamed: D11.1 (K), U3.6, U3.7
unnamed: D11.2 (A), R24.2
unnamed: D12.2 (A), R20.1
unnamed: D13.2 (A), R21.1
unnamed: D14.2 (A), R22.1
unnamed: D15.2 (A), R23.1
unnamed: D16.2 (A), R38.2
unnamed: J7.2, R33.1
unnamed: R19.2, U4.28 (PB2)
unnamed: R34.2, U6.1 (A->B)
unnamed: R35.2, U5.16 (IREF)
unnamed: R39.1, U10.9 (AD0)
ON_OFF_LIDAR: J12.1, U4.20 (PA4)
RST: C19.1, R11.2, SW1.1, U4.7 (NRST)
RST_ATM328p: C16.2, J4.3, R15.2, U2.29 (PC6)
RX_ATM328p: R1.1, U2.30 (PD0)
RX_LED: R1.2, U1.2 (TXD), U3.3
SCK_74HC245: U5.3 (SCK), U6.15 (B3), U7.5 (CLK)
SCK_ATM328p: J4.2, U2.17 (PB5), U6.5 (A3)
SPI1_CS: J9.1, U4.26 (PB0)
SPI1_MISO: J9.3, U4.22 (PA6)
SPI1_MOSI: J9.2, U4.23 (PA7)
SPI1_SCK: J9.4, U4.21 (PA5)
STM32_D+: J3.3 (D+), R17.1, U8.3 (IO2)
STM32_D-: J3.2 (D-), R16.1, U8.1 (IO1)
SWCLK: J2.3, U4.49 (PA14)
SWDIO: J2.2, U4.46 (PA13)
TX_ATM328p: R2.1, U2.31 (PD1)
TX_LED: R2.2, U1.3 (RXD), U3.5
USART1_RX: J6.3, J12.4, U4.43 (PA10)
USART1_TX: J6.2, J12.5, U4.42 (PA9)
V3: C2.1, U1.4 (V3)
VDDA: C13.1, C14.1, L1.2, U4.13 (VDDA)
Vdrive: C1.1, D1.1 (K), D2.1 (K), D9.1 (K), FB1.2, R18.1, R24.1, U1.16 (VCC), U3.8 (VCC), U8.5 (VP)
XTAL1_ATM328p: C17.1, U2.7 (PB6), Y1.1
XTAL2_ATM328p: C18.1, U2.8 (PB7), Y1.3

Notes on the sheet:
ESD
MPU6050
Distribución de la PW
MCU COMU.
MICRO SD
NRF24L01P-R
74HC245D
ATM328p
74AHC1G125

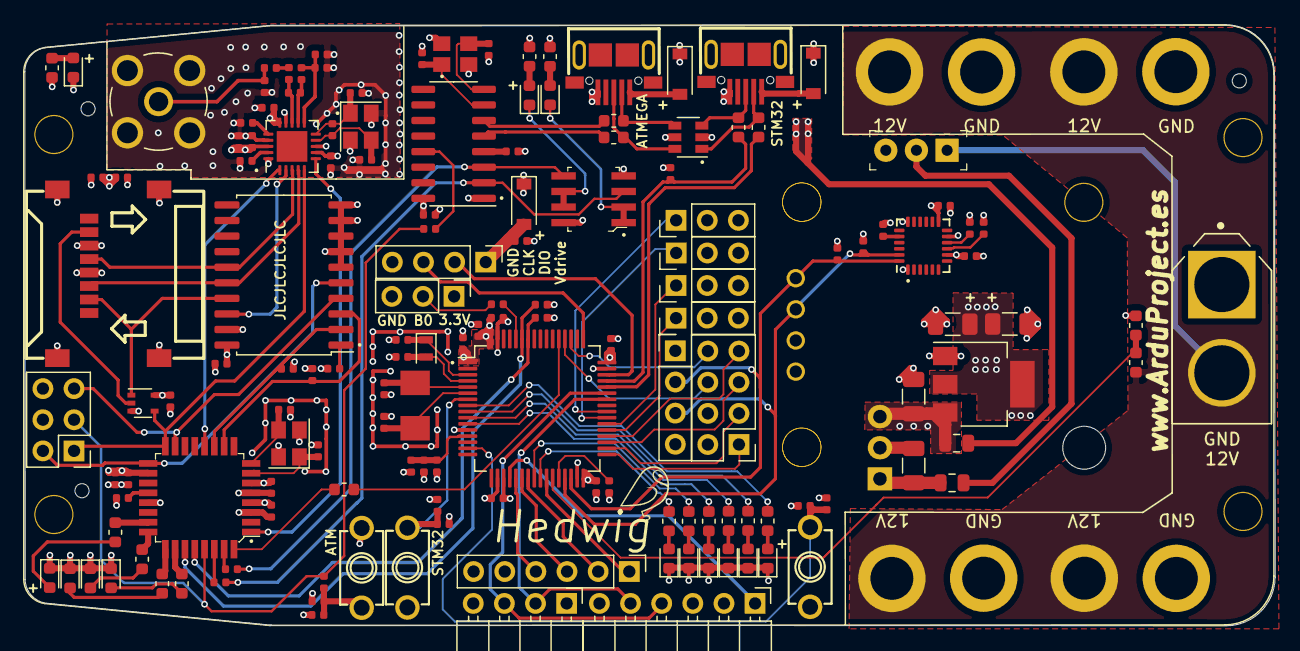
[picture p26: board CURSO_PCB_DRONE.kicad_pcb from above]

Board: 4 copper layers, 102.0 x 49.0 mm, 158 parts (1 on the bottom side), 117 nets.

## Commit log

2022-01-09 Add files via upload
    Se añade manual de montaje del PCB y del drone
2022-01-10 Add files via upload
    Se completa el documento de montaje del PCB y del drone con enlace al software de validación básica
2022-01-13 Add files via upload
    Se completa el manual de montaje
2024-01-12 Add files via upload
    Había un error y las pistas que alimentaban el PCB desde los conectaos USB no estaban tiradas.
